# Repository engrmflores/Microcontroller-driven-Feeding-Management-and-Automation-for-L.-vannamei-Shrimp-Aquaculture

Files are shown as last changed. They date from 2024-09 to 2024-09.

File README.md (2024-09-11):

# Microcontroller-driven Feeding Management and Automation for L. vannamei Shrimp Aquaculture

Shrimp is highly valued in the seafood industry by many people worldwide. 

This study aims to properly designate the correct amount of shrimp feed based on sampling the shrimp farm in proportion to the age and weight of the L. vannamei and deploy
a system that will automate the proper feed distribution through the integration of microcontrollers. 

This study also includes a pond monitoring system to ensure that the pond’s water quality is adequate for the shrimp’s cultivated health and development. 
Theresearchers compare shrimp development in culture ponds using an automated feeder and a manual feeding approach to determine the efficiency or effectiveness of the computerized feeder for
managing feeds. The growth analysis is divided into two ponds (1 and 2). 
For measuring shrimp development, the automated feeder favored pond 1, whereas pond 2 for manual feeding. 

This study found that utilizing an auto feeder increased shrimp growth rates by ensuring they were adequately fed based on the average body weight of shrimp every sampling and made them healthier by
using sensors to monitor the pond’s water quality. 

The researchers successfully developed the automated feeder and tested it many times, obtaining a total accuracy of 96.21%.

The design involved three parts of the mechanical system: the shrimp feeds container, automated supporting system, and
disseminator—the shrimp feed container designed with two parts. 
The first part is the container attached to the second part (mechanical supportive system).


Feeds Container and Disseminator System


Feeds Container, Disseminator, and Its Support


Inside the Mechanical Supporting System


Actual Design of the study


Detailed Outcomes During Culture Period

According to the findings of this study, more efficient feeding management through daily feeding quantity, effective feed distribution, and interval of feeding about the frequency
utilizing automatic feeders would promote continuous shrimp development. 
Feeding management using an automated feeder should provide the lowest FCR to maximize shrimp development and minimize feed waste accumulation at the
pond bottom. 
Increasing feed efficiency through lower FCR iscritical for shrimp farmers to reduce costs and maximize profits.

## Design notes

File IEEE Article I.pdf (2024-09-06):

1

# Microcontroller-driven Feeding Management and Automation for L. vannamei Shrimp Aquaculture

Glory Mae M. Flores [1], Elmer John C. Fernandez [1], Jerah Mae B. Ferrer [1] College of Engineering Education, Computer Engineering Program, University of Mindanao Davao City, Philippines
g.flores.441626@umindanao.edu.ph [1] e.fernandez.472620@umindanao.edu.ph [1] j.ferrer.482273@umindanao.edu.ph [1]

Abstract— Shrimp is highly valued in the seafood industry by many people worldwide. This study aims to properly designate the correct amount of shrimp feed based on sampling the shrimp farm in proportion to the age and weight of the L. vannamei and deploy a system that will automate the proper feed distribution through the integration of microcontrollers. This study also includes a pond monitoring system to ensure that the pond’s water quality is adequate for the shrimp’s cultivated health and development. The researchers compare shrimp development in culture ponds using an automated feeder and a manual feeding approach to determine the efficiency or effectiveness of the computerized feeder for managing feeds. The growth analysis is divided into two ponds (1 and 2). For measuring shrimp development, the automated feeder favored pond 1, whereas pond 2 for manual feeding. This study found that utilizing an auto feeder increased shrimp growth rates by ensuring they were adequately fed based on the average body weight of shrimp every sampling and made them healthier by using sensors to monitor the pond’s water quality. The researchers successfully developed the automated feeder and tested it many times, obtaining a total accuracy of 96.21%.

Index Terms— Feeding Management, Automation, Automated Feeder, Microcontroller-driven Feeding Management, Automatic Feeder with Pond Monitoring System

I. INTRODUCTION
Since shrimp aquaculture began in the Philippines in the 1980s, the Philippines has become one of Asia's leading shrimp producers. In December 2013, the Philippines' Bureau of Fisheries and Aquatic Resources (BFAR) registered 271 brackish water shrimp farms (with a total area of 3,617.8 ha) [1].
Penaeus monodon (Tiger Prawn) and L. vannamei (Pacific White Shrimp) are the two most common farmed shrimp varieties. Penaeus monodon, also known as P. monodon, is grown in 48 percent (1,772.6 ha) of the country's shrimp farms. The L. vannamei is cultivated on 27% (909.4 ha) of shrimp farms, while other shrimp varieties, including the Endeavor shrimp, are grown on the remaining 25% (935.8 ha). Due to the difficulties of raising P. monodon, farmers have shown an interest in cultivating pacific white shrimp. Disease issues have afflicted the P. Monodon culture, and farmers have had trouble finding pathogen-free seeds. Rising feed and electricity prices are also issues. Because of its resistance to specific diseases, low nutrient demand, and competitive rates in the domestic market, the species L. vannamei is attractively marketable [2]. Due to its higher growth rate of 1.0 to 1.5 grams (g) per week relative to P. monodon's growth rate of 1 g/week, many farmers in the Philippines are now choosing L. vannamei over P. monodon. L. vannamei shrimp are often more standardized in size at harvest, eliminating the need for sorting before distribution to the market [3]. Several factors, such as the harvest ton, mean body weight, survival rate, and feed conversion ratio, can all be used to quantify shrimp growth and production. According to previous research, the shrimp feed conversion ratio should be proportional to their mean body weight [4]. This variety of shrimp also consumes feed regardless of light and dark conditions, according to research that looked at the feeding pattern of L. vannamei [5]. Floods, typhoons, and monsoon rains may all significantly impact shrimp farming. Shrimp development has slowed, disease resistance has increased, and mass fatality has occurred because of pollution from watershed activities and self-generated organic load [6]. The shrimp aquaculture industry depends upon the proper feeding and harvesting techniques. The first step in appropriate feed management at the farm level is choosing and buying a feed that will expand production under the cultivated shrimps [7]. Traditionally, the shrimp needs to feed 1-4 times a day. Still, the advent of automated feeders has enabled farmers to increase the number of feedings without raising the labor needed [8]. However, Ullman et al. (2018) presented that feeding six times compared to 2 times increased significantly. Theoretically, increased feeding frequency results in higher nutritional feed content because nutrient leaching is reduced [9].
The nutritional performance of a shrimp feed depends upon five interconnected factors, namely: the nutrient content and composition of the diet fed, the physical properties and water stability of the diet provided, the transportation and storage of the diet before giving feed on the farm, the feeding method employed for feed application and usage on the farm; and the farming system, stocking density, water management, and availability of natural foods [10]. Shrimp feeding is essential to avoid losing profits due to the high cost of shrimp feeds. It can minimize feed cost in L. vannamei culture. The feed conversion

2

ratio would be low for the duration of cultivation by appropriately implementing the prescribed feeding guide and selecting the proper feed to utilize. However, the variability in behavior and feeding patterns of shrimp raised in shrimp culture ponds is still poorly known. Adopting good feed management practices will help to reduce water quality problems and increase shrimp production success. Diets are used in semi-intensive cultures to boost production beyond the pond's natural productivity standards, which can take up to 85 percent of the shrimp's diet. However, it's crucial to specify how feeding rates affect survival, weight gain, growth, productivity per hectare, and the total biomass [11]. According to Fox et al. (2001), The farmer will apply the feed regularly and only in the amount consumed rapidly to maximize growth and minimize waste. Historically, farmers applied the feed; consumption tracked using manual labor to spread and inspect feeding trays [12]. Automatic feeders are becoming more popular because of their ability to provide more feedings per day while requiring less labor than manual feeding [13]. Another advancement is using hydrophones to track the shrimp's feeding response in the pond to assess the feeding activity and then provide based on that response [14]. All these technological advancements can benefit both productivity and water quality.

This study aims to properly designate the correct amount of shrimp feed based on sampling the shrimp farm in proportion to the age and weight of the L. vannamei and deploy a system that will automate the proper feed distribution through the integration of microcontrollers. It also includes a pond monitoring system to ensure that the ponds’ water quality is adequate for the shrimp’s health and development while cultivating.
This application will help the shrimp industry of the Philippines to maintain the ranks of worldwide shrimp aquaculture by helping shrimp farmers be more efficient and technologically precise through accumulated data of feeding practice. This study will reduce the cost of cultivating shrimp farms by ensuring that overfeeding, feeding waste, and water and soil quality deterioration will not improve shrimp development. This new project will be a milestone in technology and aquaculture. This study would become an excellent reference for future computer engineers dealing with the fusion of aquaculture and technology.
For this study, the preferred feed for L. vannamei is Blanca Vannamei Feeds from Charoen Pokphand. Foods Philippines Corporation. The meal provides precise essential amino acids, vitamins, minerals, and other vital nutrients for optimum growth and enhanced immunity against stress. This preferred feed is according to the product guide given by manufacturers [15].
The extent of this research covers the classification of the current weight and age of the shrimps in correlation to the correct feeding guide of the preferred brand by local farmers. This research also covers the automation of the feeding process but not in real-time. This system is a prototype and will not be industrial-sized. The stocking of feed will be done manually and not include the harvesting process.

II. MATERIALS AND METHODS
For this study, applied research is an outline for the whole duration. It aims to develop a system that will determine the correct amount of shrimp feed and automate the feeding process via microcontroller data comparison and manipulation. For the development of the system, knowledge in circuitry, electronics, and microcontroller programming is involved.
A. Conceptual Framework

Fig. 1 shows the conceptual framework of the study. The input is the weight of the shrimp concerning the age of the shrimp. It will undergo the process of the pond monitoring system that determines the water temperature, pH acidity, and water level of the pond. Determining the feed amount and feeding schedule based on the input and conditions of the software. These processes will yield a system that automates proper feed distribution.

INPUT | PROCESS | OUTPUT

Fig. 1 Conceptual Framework

B. Material and Resources

The design involved three parts of the mechanical system: the shrimp feeds container, automated supporting system, and disseminator—the shrimp feed container designed with two parts. The first part is the container attached to the second part (mechanical supportive system). Fig. 2 shows the whole system.

The shrimp feed container is made of a steel plate 0.8 mm thick, 12 x 10 inches in width, and 17 inches in height. The feed container can have 2 kg feeds in it. The researchers used Visual Studio software to design the research's user interface, and a series of codes will be implemented using the VB.NET language. All codes from the pond monitoring system to an automated feeder will be coded separately to quickly detect software errors when debugging and troubleshooting. The proponents built the device with a steel container with an acrylic glass design to ensure good feed storage. The feed’s vitamins, minerals, and other essential nutrients will not be degraded and help deter birds and pests.

-Pond Monitoring

-Feed Amount

-Schedule
Allocation

-Automated
Feed
Distribution

-Weight

-Age of
Shrimps

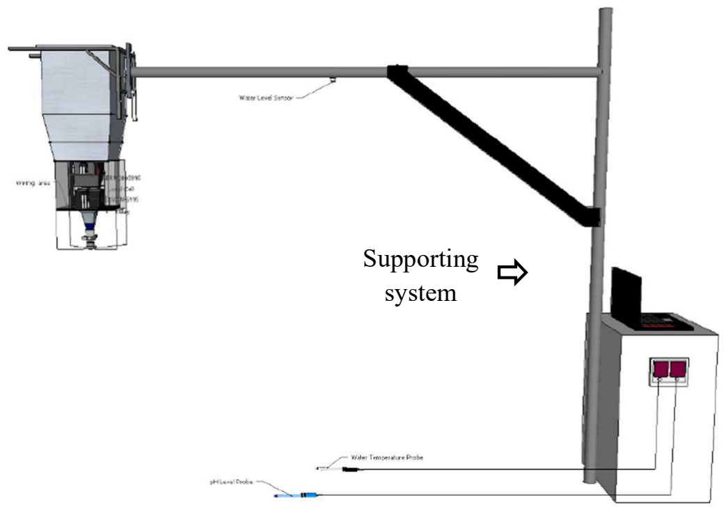
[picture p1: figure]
Supporting system

3

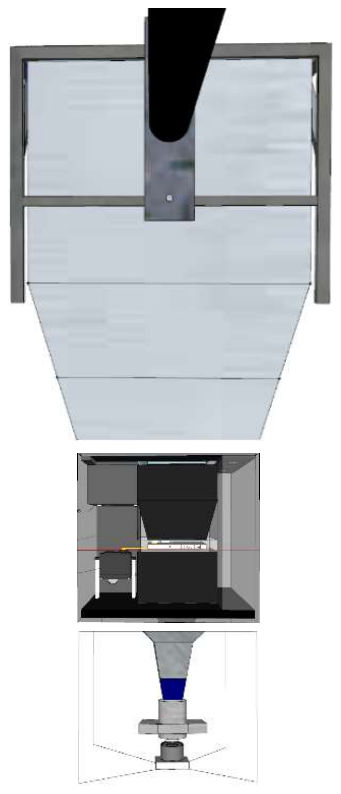
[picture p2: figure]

Fig. 2 Feeds Container and Disseminator System

The mechanical supporting system is divided into two parts. The first part is the first servo motor that holds the plate to control the feeds going to the second part. The second part is the second servo motor that carries the load cell to manage the number of meals before disseminating. Fig. 3 shows the mechanical supporting system attached to the bottom part of the container.
The researchers installed CZL639HD loadcell to properly weigh the feeds given to the shrimps in time of feeding based on the average body weight of every sampling.

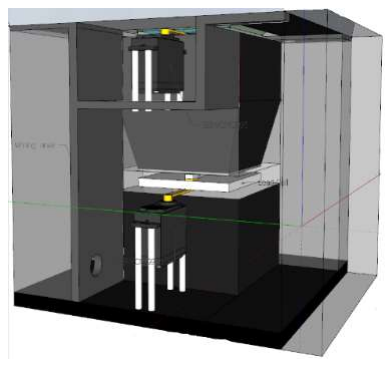
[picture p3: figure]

Fig. 3 Inside the Mechanical Supporting System

To install the automated feeder in the L. vannamei pond needs a supporting system. All mechanical systems shown in Fig. 2 are attached to the support system shown in Fig. 4.
The supporting system has two poles. The first pole is about 19.6 ft (6m) long and is buried about 6 ft (2m) in the ground, while the second pole that holds the feed container is about 6 meters long. The circuits were placed in the small box beside the system unit for the pond monitoring. The automated feeder is connected and will work using the laptop and the program installed in the software. The 5 volts dc motor speed can be controlled by manipulating the 5 volts two-channel relay installed in the Arduino Mega, and it is operated from 0 up to 1,000 rpm. With this variable speed, the distance of feed throwing can cover all the vital areas of the pond.

Fig. 4 Feeds Container, Disseminator, and Its Support

The software system also continuously determines the pond's water temperature, pH acidity, and water level using the Arduino Uno placed inside the box. For water temperature, the system utilized a DS18B20 sensor, Arduino pH sensor for pH acidity, and ultrasonic sensor for water level; near the supporting system of the device placed the package. The system block diagram for monitoring the shrimp production habitat's water quality is shown in Fig. 5.

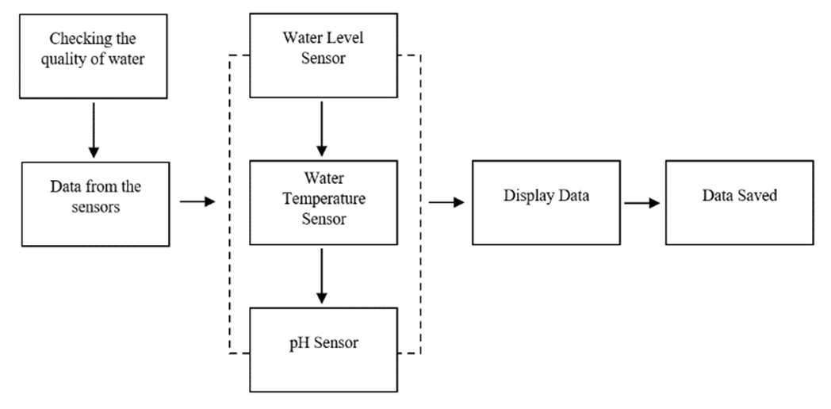
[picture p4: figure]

Fig. 5 Block Diagram of Pond Monitoring

C. System Flow
First, a sample L. vannamei shrimp will be weighed. After the weight is determined, the system will cross-reference it with the feeding guide and the cycle schedule of the aquaculture. The flow will result in getting the precise feed amount and schedule. After this, the automatic feeding process will commence by the program using the manipulation of the microcontrollers and relays to control the mechanical part of the system. Then the system will display the current activity status of the feeder. It will also prompt for feed. Stock refill when necessary. Fig. 6

Shrimp
feeds
container

Mechanical
supporting
system

Disseminator
system

First Part of
Mechanical System

Second Part of
Mechanical System

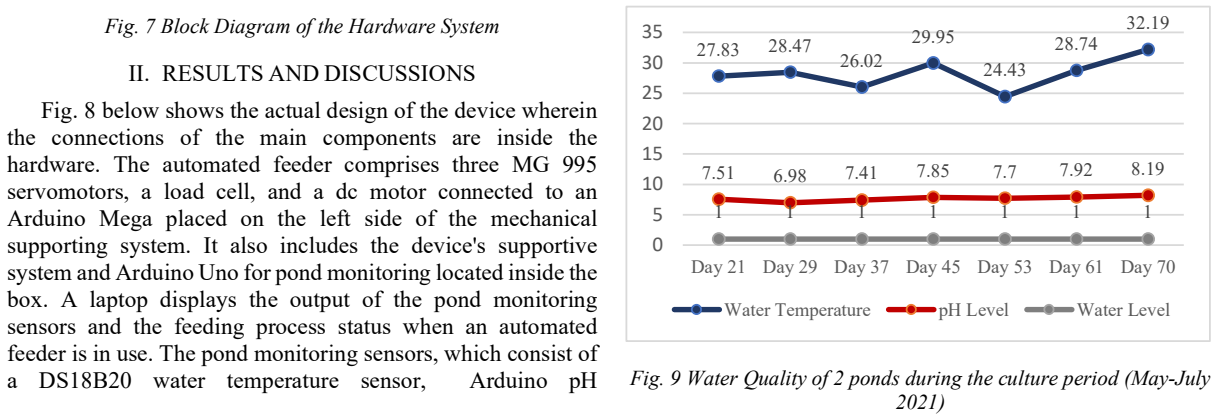
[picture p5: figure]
Water Temperature; pH Level; Water Level; II. RESULTS AND DISCUSSIONS; a DS18B20 water temperature sensor,; Arduino pH

4

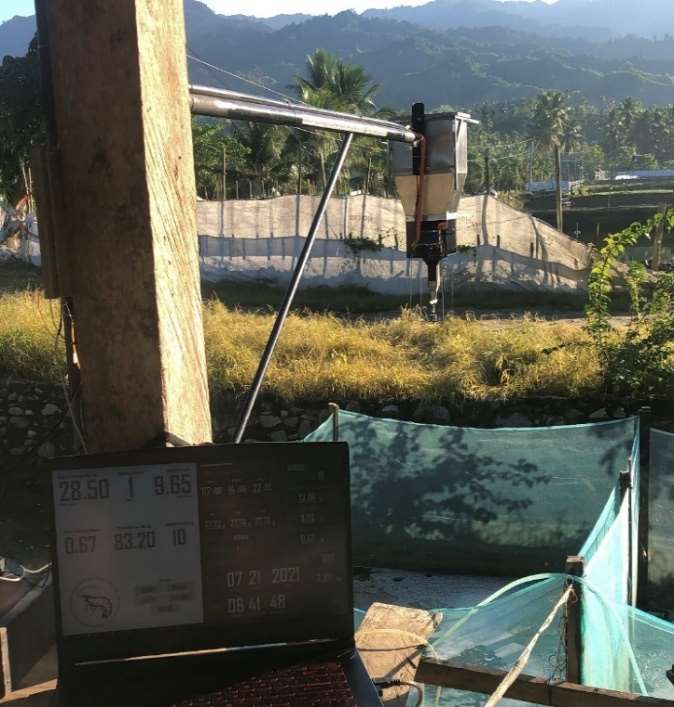
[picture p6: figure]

Day 21 Day 29 Day 37 Day 45 Day 53 Day 61 Day 70 below illustrates the system's flow to accomplish the study's objectives.

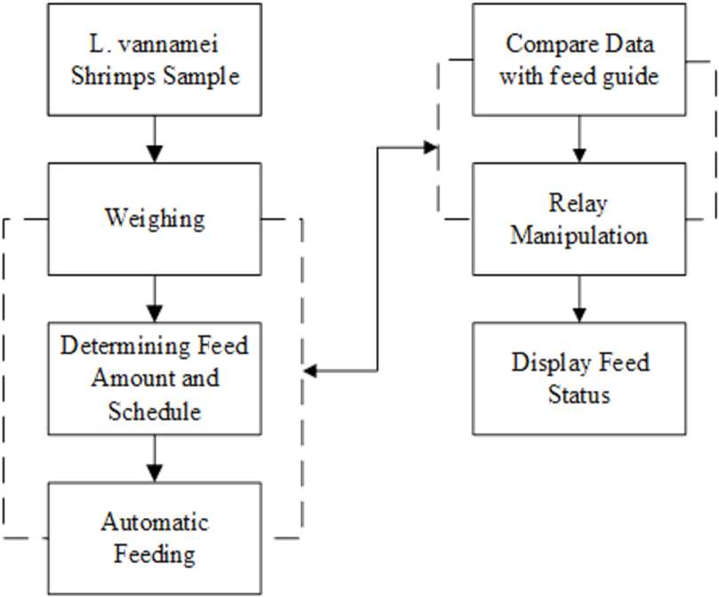
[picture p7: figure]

Fig. 6 Device System Flow
The research object was created using tools made with an Arduino Uno and equipped with a temperature sensor to measure pond water temperature, a pH sensor to measure pH balance, and a 0-100g loadcell to determine the weight of the shrimps to be sampled. The automatic feeder connects to the Arduino Mega, equipped with an ultrasonic sensor to measure water level and a 0-100g to determine feed weight. Fig. 7 below illustrates the flow of the hardware system.

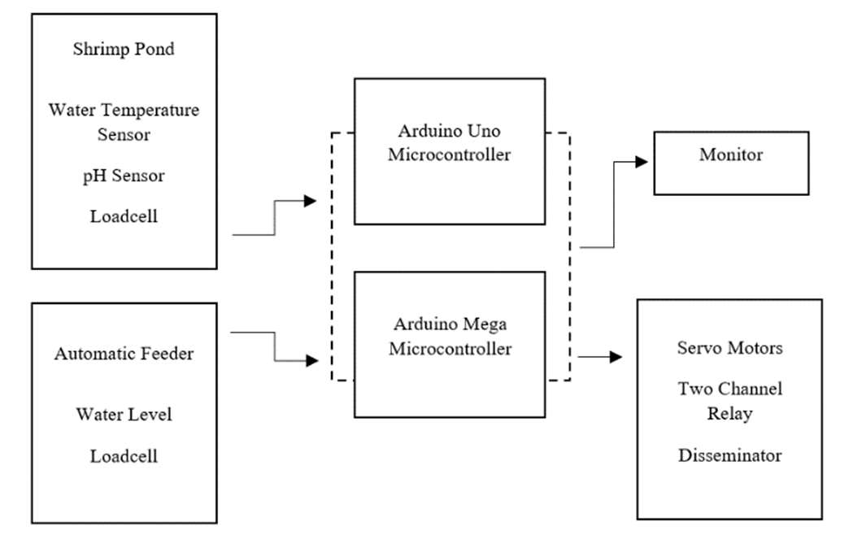
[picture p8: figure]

Fig. 7 Block Diagram of the Hardware System

Fig. 8 below shows the actual design of the device wherein the connections of the main components are inside the hardware. The automated feeder comprises three MG 995 servomotors, a load cell, and a dc motor connected to an Arduino Mega placed on the left side of the mechanical supporting system. It also includes the device's supportive system and Arduino Uno for pond monitoring located inside the box. A laptop displays the output of the pond monitoring sensors and the feeding process status when an automated feeder is in use. The pond monitoring sensors, which consist of sensor/meter kit, and an Arduino ultrasonic, are used to monitor the pond's water quality to ensure shrimp's health and development while being cultivated.

Fig. 8 Actual Design of the study The researchers compare shrimp development in culture ponds using an automated feeder and a manual feeding approach to determine the efficiency or effectiveness of the computerized feeder for managing the feeds. The experiment was conducted at Kitagas, Sarangani Province, from May 22, 2021, to July 31, 2021. The growth analysis is divided into two ponds (1 and 2). Pond 1 measures shrimp development using an automated feeder, whereas pond 2 uses manual feeding. Water quality parameters in the culture ponds are shown in Fig. 9. The system device will automatically record the water level, water temperature, and pH value for the water quality of both ponds every after seven days. The pond water temperatures ranged between 27—83 ℃ and 32.19 ℃. The pH value of both ponds ranged between 7.51 and 8.19.

Fig. 9 Water Quality of 2 ponds during the culture period (May-July

5

Fig. 10 below shows the number of shrimps that survived by the stocking population. The researchers determined the total number of mortalities for the automated pond and manual pond after 70 days of cultivation. Out of 200 pcs, the number of shrimps survived in automatic feeding is 177, while manual feeding is 135.

Fig. 10 The Graph of Number of Shrimps Survived about the Shrimp Population

Fig. 11 below shows the natural survival rate for automated feeding, which is 88.5%, with a total mortality rate of 11.5% compared to the survival rate for manual feeding is 67.5%, which has a real mortality rate of 32.5%. Pond 1 had a 21% better survival rate compared to pond 2.

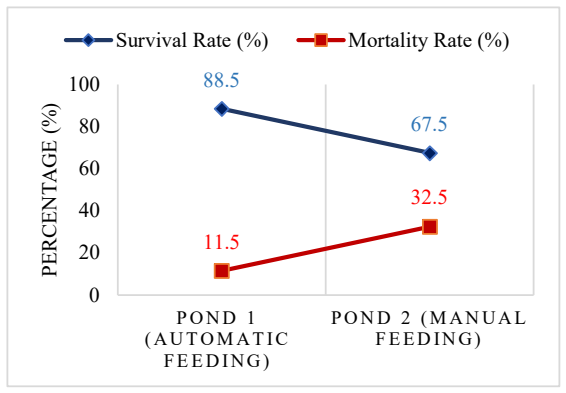
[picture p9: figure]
F E E D IN G) PERCENTAGE ⁽%⁾; Survival Rate (%); Mortality Rate (%)

Fig. 11 The Graph for Survival Rate and Mortality Rate

The outcomes of shrimp development achieved throughout the culture period are detailed in (Table 1). Regardless of the feeding period, greater feed levels improved average body weight, survival, biomass, and production output. The automatic feeder utilized pond demonstrated higher average body weight growth after 70 days of cultivation, although the FCR was very good compared to the manual feeding pond.

Table 1: Detailed Outcomes During Culture Period.

Parameters

Pond 1
(Automatic
Feeder)

Pond 2
(Manual
Feeding)
Area (m) | 2 x 2.5 | 2 x 2.5
Stocking (pcs) | 200 | 200
Stocking Date | May 22, 2021 | May 22, 2021
Harvest Date | July 31, 2021 | July 31, 2021
Culture Period (d) | 70 | 70
Average Body
Weight (g)

20.01 19.96

Number of Shrimps
Survived (pcs)

177 135

Survival Rate (%) | 88.5 | 67.5
Mortality Rate (%) | 11.5 | 32.5
Shrimp Biomass
(kg)

3.542 2.695

Total Feed Used
(kg)

3.615 3.623

FCR | 1.02 | 1.34

Fig. 12 below shows the result of standard and experimental feed from the device given to the shrimps every seven days.

Fig. 12 Graphical Statistical Analysis

The study shall be using the t-test analysis in which the control group will be the standard computed value of the amount of feed. In contrast, the experimental group will be the feed generated by the feeding system produced in this study. The researchers obtained a total accuracy of 96.21% based on the calculation provided by the standard t-test formula. Therefore, the shrimp’s weight after 70 days of cultivation using manual feeding and the feeding device are not equal. There is a significant difference between the feed amount generated using manual feeding and the feed amount generated

by the feeding system. ⁴¹⁰.88 | 406.8 | 535.04 | 606.04 | 718.32 | 962.6 412.5 | 402.81 | 529.31 | 602.22 | 714.15 | 962.15
D A Y 2 1 | D A Y 2 9 | D A Y 3 7 | D A Y 4 5 | D A Y 5 3 | D A Y 6 1 - 7 0
Standard Feed | Experimental Feed
Pond 1 (Automatic Feeding) | Pond 2 (Manual Feeding)
Stocking (pcs) | 200 | 200
Number of Shrimps Survived (pcs) | 177 | 135

200 200 177
| 135

0

50

100

150

200

250

Stocking (pcs) Number of Shrimps Survived (pcs)

6

III. CONCLUSIONS AND FUTURE WORKS

According to the findings of this study, more efficient feeding management through daily feeding quantity, effective feed distribution, and interval of feeding about the frequency utilizing automatic feeders would promote continuous shrimp development. Feeding management using an automated feeder should provide the lowest FCR to maximize shrimp development and minimize feed waste accumulation at the pond bottom. Increasing feed efficiency through lower FCR is critical for shrimp farmers to reduce costs and maximize profits. The shrimp growth, survival rate (SR), and feeding efficiency were satisfactory during the culture phase. Overall, utilizing an automated feeder provides a healthier shrimp by improving water quality, ensuring continuous feeding, and avoiding overfeeding. Improved water quality, appropriate feeding management, and installing pond monitoring sensors reduce the danger of mortality or disease breakout, resulting in higher profitability and lower labor and production expenses.
For future development, adding specific modules and sensors may enhance or expand the dimension and material of an automated feeder. For pond monitoring, we recommend adding water quality parameters such as dissolved oxygen (DO sensor), water salinity sensor, and alkalinity sensor to maintain the excellent water quality of the pond, which enables shrimps to develop faster. In addition to future automated feeder development for feeding management, we suggest installing a sensor to detect the state of feeds within the container, whether empty or complete, and sending the information via the Global System for Mobile Communications (GSM Module).

REFERENCES

[1] C. Vergel, “Current Trends in the Philippines’ Shrimp Aquaculture industry: A Booming Blue Economy in the Pacific,” Oceanography & Fisheries Open access Journal, vol. 5, no. 4, 2017. Available: 10.19080/ofoaj.2017.05.555668.
[2] C. Caipang J. Geduspan and M. Muegue, “Current status of shrimp aquaculture in the Philippines,” Biotechnological Advances in Shrimp Health Management in the Philippines, vol. 1, no. 1, 2015. Available: https://www.trnres.com/ebook/uploads/caipangivcontent/T_14370388 41Caipang%201.pdf. [Accessed 25, November 2019].
[3] “Effective Vannamei Culture Practices”, Agriculture Monthly, 2019. [Online]Available:
https://www.agriculture.com.ph/2019/05/01/effective-vannamei-culture-practices/. [Accessed: 25- Nov- 2019].
[4] N. Azz, M. Misiran, T. S. Yin, T. H. Yee, N. J. Hui, L. Y. Pei, N. I. Mahat, M. M. Ysof, and A. S. Ruddin, “The Effect of Climate Change to the Farm Shrimp Growth and Production: An Empirical Analysis,” International Journal of Engineering & Technology, vol. 7, no. 4.1, p. 138, Dec. 2018.
[5] N. Sanudin, A. Tuzan and A. Yong, “Feeding Activity and Growth Performance of Shrimp Post Larvae Litopenaeus vannamei Under Light and Dark Conditions,” Journal of Agricultural Science, vol. 6, no. 11, 2014. Available: 10.5539/jas.v6n11p103.
[6] Corre Jr., V. (1993). The shrimp farming industry in the Philippines. In C.T. Villegas, M.T. Castaños, & R.B. Lacierda (Eds.) Proceedings of the Aquaculture Workshop for SEAFDEC/AQD Training Alumni, 8-11 September 1992, Iloilo, Philippines (pp. 88-103). Tigbauan, Iloilo,

Philippines: Aquaculture Department, Southeast Asian Fisheries Development Center.
[7] H. E. Quintero and L. A. Roy, “Practical feed management in semi-intensive systems for shrimp culture,” The Shrimp Book, pp. 443–454.
[8] C. Ullman, M. A. Rhodes, and D. A. Davis, “Feed management and the use of automatic feeders in the pond production of Pacific white shrimp Litopenaeus vannamei,” Aquaculture, vol. 498, pp. 44–49, 2019.
[9] L. N. Jescovitch, C. Ullman, M. Rhodes, and D. A. Davis, “Effects of different feed management treatments on water quality for Pacific white shrimp Litopenaeus vannamei,” Aquaculture Research, vol. 49, no. 1, pp. 526–531, Apr. 2017.
[10] A.G Tacon, D. Jory, A. Nunes, “Shrimp feed management: issues and perspectives.”, On-farm feeding and feed management in aquaculture 583, 2013: 481-488.
[11] C. Antunes, C. Ledo, C. Pereira and J. Santos, “Evaluation of Feeding Rates in The Production of Litopenaeus Vannamei Shrimp using Artificial Substrates”, Ciência Animal Brasileira, vol. 19, no. 0, 2018. Available: 10.1590/1809-6891v19e-50805 [Accessed 27 November 2019].
[12] Fox, J., G. D. Treece, and D. Sanchez. 2001. Shrimp nutrition and feed management in M.C. Hawsand C.E. Boyd, editors. Methods for improving shrimp farming in Central America. University of Central America Press, Managua, Nicaragua.
[13] Jory, D. E. 2016. The proper feed management of commercial shrimp feeds, part2. Global Aquaculture Advocate, Portsmouth, New Hampshire, USA.
[14] Bador, R., P. Blyth, and R. Dodd. 2013. Acoustic control improves feeding productivity at shrimp farms. Global Aquaculture Advocate 77–78 and Napaumpaiporn, T., N. Chuchird, and W. Taparhudee. 2013. Study on the efficiency of three different feeding techniques in the culture of Pacific white shrimp (Litopenaeus vannamei). Kasetsart University Fisheries Research Bulletin 37:8–16.
[15] https://www.cpfworldwide.com/en/media-center/industrial-1335

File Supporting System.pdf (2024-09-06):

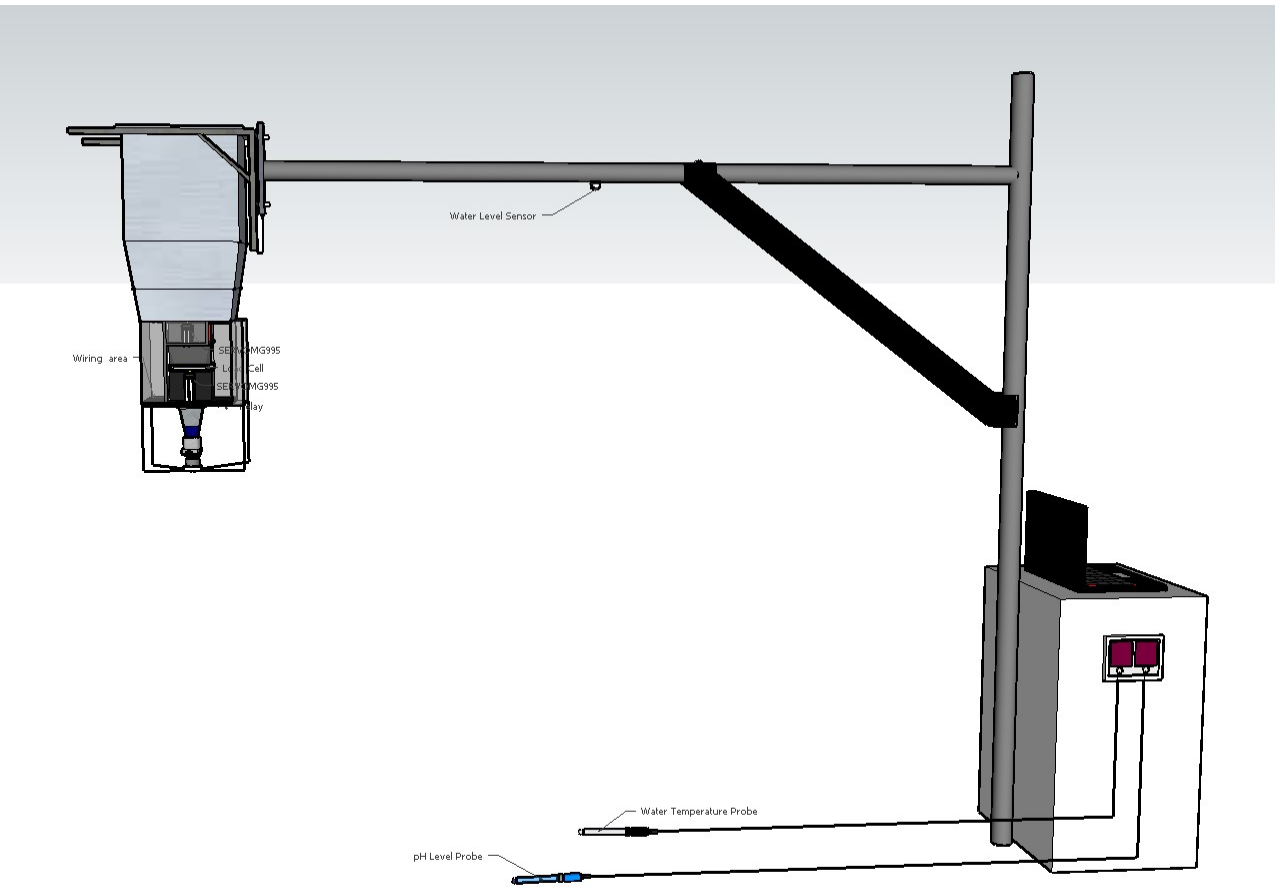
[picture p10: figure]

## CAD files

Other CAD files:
System Design Sketch.skp

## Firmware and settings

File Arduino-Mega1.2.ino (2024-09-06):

#include <OneWire.h>
#include <DallasTemperature.h>
#include <U8glib.h>
#include <stdlib.h>
#include <HX711_ADC.h>
#include <EEPROM.h>
#include<Servo.h>
String Final_Values;

#define relay 8//****************************

//**********ULTRASONIC SENSOR**********
#define echoPin 4
#define trigPin 5

//**********LOAD CELL**********
const int HX711_dout = 7; //mcu > HX711 dout pin
const int HX711_sck = 6; //mcu > HX711 sck pin

HX711_ADC LoadCell(HX711_dout, HX711_sck);
const int calVal_eepromAdress = 0;
long t;
float final_Weight1;

//**********ULTRASONIC SENSOR**********
long duration;
int distance; 

//**********SERVO MOTOR**********
Servo S_Motor1;
Servo S_Motor2;
Servo S_Motor3;
int var = 0;

void setup() 
{
 pinMode(trigPin, OUTPUT);
  pinMode(echoPin, INPUT);
  pinMode(relay, OUTPUT);
  digitalWrite(relay, HIGH);

  S_Motor1.attach(13);
  S_Motor1.write(125);
  S_Motor2.attach(12);
  S_Motor2.write(150);
  S_Motor3.attach(11);
  S_Motor3.write(90);

  Serial.begin(57600);

  LoadCell.begin();
  float calibrationValue; // calibration value (see example file "Calibration.ino")
  calibrationValue = 696.0; // uncomment this if you want to set the calibration value in the sketch
  #if defined(ESP8266)|| defined(ESP32)
  //EEPROM.begin(512); // uncomment this if you use ESP8266/ESP32 and want to fetch the calibration value from eeprom
  #endif
  EEPROM.get(calVal_eepromAdress, calibrationValue); // uncomment this if you want to fetch the calibration value from eeprom
  long stabilizingtime = 2000; // preciscion right after power-up can be improved by adding a few seconds of stabilizing time
  boolean _tare = true; //set this to false if you don't want tare to be performed in the next step
  LoadCell.start(stabilizingtime, _tare);
  if (LoadCell.getTareTimeoutFlag()) {
    //Serial.println("Timeout, check MCU>HX711 wiring and pin designations");
    while (1);
  }
  else {
    LoadCell.setCalFactor(calibrationValue); // set calibration value (float)
    //Serial.println("Startup is complete");
  }
}

void loop() 

{ 
  //**********ULTRASONIC SENSOR**********
   //Clears the trigPin condition
 digitalWrite(trigPin, LOW);
  delayMicroseconds(2);
   //Sets the trigPin HIGH (ACTIVE) for 10 microseconds
  digitalWrite(trigPin, HIGH);
  delayMicroseconds(10);
  digitalWrite(trigPin, LOW);
   //Reads the echoPin, returns the sound wave travel time in microseconds
  duration = pulseIn(echoPin, HIGH);
   //Calculating the distance
  distance = duration * 0.034 / 2; // Speed of sound wave divided by 2 (go and back)
   //Displays the distance on the Serial Monitor

  if (var == 1) //**********************
  {
    S_Motor3.write(30);
    delay(250);
  }
  
  if (var == 1)//**********************
  {
    S_Motor3.write(90);
    delay(250);
  }
  //**********LOAD CELL**********
  for(int a = 0 ; a<=1000 ; a++)
  {
    static boolean newDataReady = 0;
    const int serialPrintInterval = 0; //increase value to slow down serial print activity

    //check for new data/start next conversion:
    if (LoadCell.update()) newDataReady = true;

   // get smoothed value from the dataset:
    if (newDataReady) 
    {
      if (millis() > t + serialPrintInterval) 
      {
        float i = LoadCell.getData();
        //Serial.print("Load_cell output val: ");
        //Serial.println(i);
        final_Weight1 = i;
      newDataReady = 0;
      t = millis();
     }
    }
      }

      if (var == 1)//**********************
  {
    S_Motor3.write(150);
    delay(250);
  }

  int val = Serial.read() - '0';
  
  if(val == 1) // Fist Motor_Opening
  {
    S_Motor1.write(115);
    var = 1; 
  }

  else if(val == 2 ) // Fist Motor_Closing
  {
   
     S_Motor1.write(125);
     S_Motor3.write(90);
     var = 0;
  }

  else if (val == 3) //Second Motor_Opening
  {
    S_Motor2.write(55);
    digitalWrite(relay, LOW);
    delay(100); 
  }

  else if (val == 4) //Second Motor_Closing
  {
    S_Motor2.write(150);
    digitalWrite(relay, HIGH);
  }

  if (var == 1)//**********************
  {
    S_Motor3.write(90);
    delay(250);
  }
distance = 1;
 Final_Values = Final_Values + distance + "," + final_Weight1 + ",";
    //Final_Values = Final_Values + distance + "," + phValue + ",";
  Serial.println(Final_Values);

Final_Values = "";

if (var != 1)
  {
  delay(500);
  }
  }
  
  
  

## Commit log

2024-09-11 Add files via upload
    Source code for Arduino-Mega
2024-09-11 Source code for Arduino-Mega
2024-09-11 Source code for Arduino-Uno
